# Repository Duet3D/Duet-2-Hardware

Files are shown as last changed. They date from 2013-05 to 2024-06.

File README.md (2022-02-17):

# Duet-2-Hardware

The Duet 2 3D Printer Controller design files repository.

For hardware ourhcases see https://www.duet3d.com/

Duet Hardware runs RepRapFirmware:
https://github.com/Duet3D/RepRapFirmware

Documentation:
https://docs.duet3d.com/Duet3D_hardware/Duet_2_family

## Duet 2 Wifi and Duet 2 Ethernet

Design by Tony Lock and David Crocker
More info:
https://www.duet3d.com/
LICENSE: see the LICENSE file in the repository

## Duet 0.8.5

Design by Tony Lock, based on the Duet 0.6
More info here:
http://blog.think3dprint3d.com/2015/08/new-duet-electronics-version-085.html
LICENSE: http://www.ohwr.org/attachments/2388/cern_ohl_v_1_2.txt

## Duet 0.6:
Design by Andy Hingston, Tony Lock, Adrian Bowyer with much advice from Chris Palmer.
More info here:
http://blog.think3dprint3d.com/2013/12/Duet-Arduino-Due-compatible-3DPrinter-controller.html
LICENSE: http://www.ohwr.org/attachments/2388/cern_ohl_v_1_2.txt

Developed in KiCAD: http://www.kicad-pcb.org/display/KICAD/KiCad+EDA+Software+Suite

## Support requests

Please use the [forum](https://forum.duet3d.com) for support requests.

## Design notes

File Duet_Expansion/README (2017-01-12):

For info on the Duex2/5 see:
https://duet3d.com/wiki/Duex2_and_Duex5_Features

For more info on the Duex4 expansion board see:
http://blog.think3dprint3d.com/2015/04/duex4-v02a-minor-updates.html

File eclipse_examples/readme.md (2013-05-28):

Example Eclipse projects for Arduino Due 

Eclipse version Juno SR1, CDT 8.1.1

ArduinoDueCore should be in the Eclipse Workspace along with other 
Eclipse Due projects which reference this Core project - this allows
for easily debugging by following what core functions do.

The DueTemplate project is a simple "hello world"/blink project which
is easy to copy and adapt for other projects as it is setup with the
required libraries and toolchain directories

The SD_HSMCI_TEST project provides the same functionality as the
hsmci_example sketch within ..\test_sketches\hsmci_example. It writes
and reads a number of test files to an SD card.

The steps to integrate Due into Eclipse is based on the forum posts
here:
http://forum.arduino.cc/index.php/topic,135403.0.html
especially the posts by Nassarane

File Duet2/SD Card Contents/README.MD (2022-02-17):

This is the SD card contents distributed with Duet Generation 2 (Duet Wifi and Duet Ethernet) boards as at May 2019

The SD card contents are only a starting point and the files in the /sys directory should be updated to match a specific printer configuration. A good start point for this is the RepRapFirmware configurator:

https://configtool.reprapfirmware.org/

For more information on the SD card structure check:
https://docs.duet3d.com/en/User_manual/RepRapFirmware/SD_card

For updating the firmware this is a good start point:
https://docs.duet3d.com/en/User_manual/RepRapFirmware/Updating_firmware

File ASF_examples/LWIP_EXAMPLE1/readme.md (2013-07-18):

Example ATMEL Studio 6.1 project for using the SAM3X8E and the KSZ8051RNL PHY
Modifications by tony@think3dprint3d.com, Based on the Atmel Studio Framework example
project for LWIP on the SAM3X8H development board.

All code (c) the respective owners as noted in the header files.

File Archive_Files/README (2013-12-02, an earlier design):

Note about the archive files specifically.

These files consist of test programs for Arduino IDE, Eclipse and Atmel Studio Framework. They are mainly based on example code from ASF, along with some original work by Tony@think3dprint3d.com. Where not specified they are licensed under the GPL v3.0 (but the vast majority has specified licenses from ASP or elsewhere).

Quite a lot of these programs and bits of code were designed to work on older versions of the DUET and may not work with the current version.
Tony Lock
blog.think3dprint3d.com

--------------------

Duet test arduino code in \test_sketches, libraries for duet specific peripherals in \libraries (now out of date)

The LwIP example has only been tested in Atmel Studio 6 and is adapted from the SAM3X-EK example
in the Atmel Studio Framework. It sets up a basic TCP/IP stack which responds to ping and serves
a single webpage on 192.168.0.100

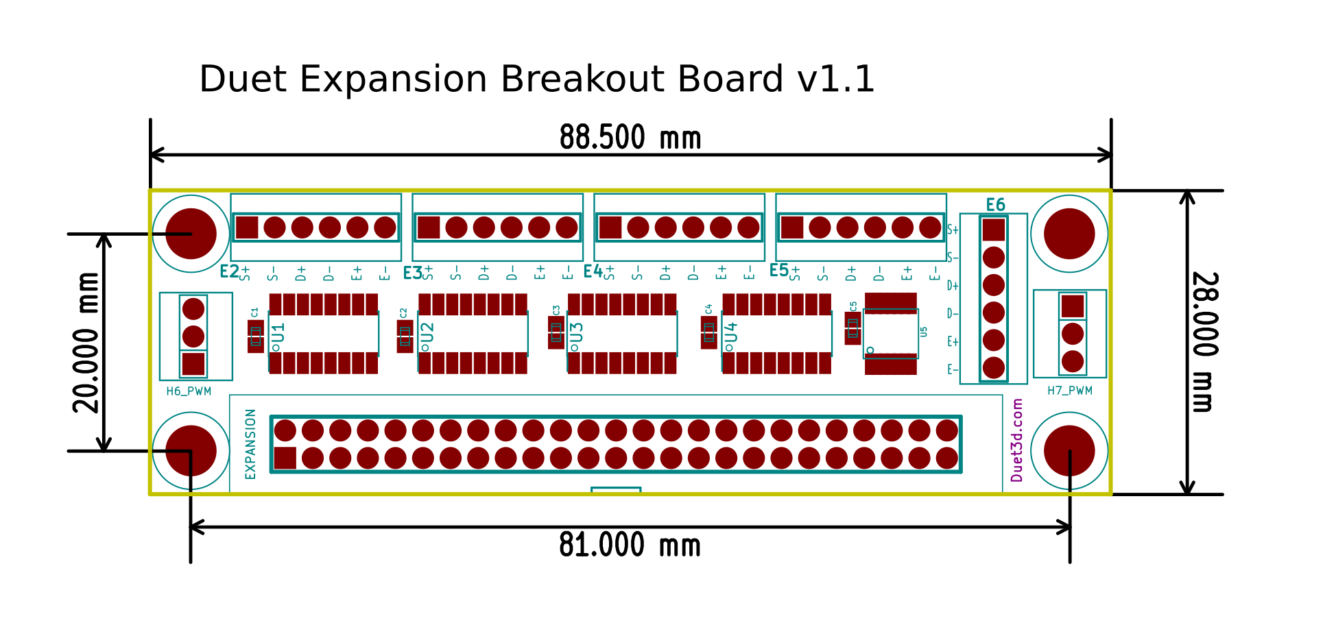
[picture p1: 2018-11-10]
Duet_Expansion/Expansion_Breakoutv1.1/ExpBreakoutv1.1_Dimensions.png

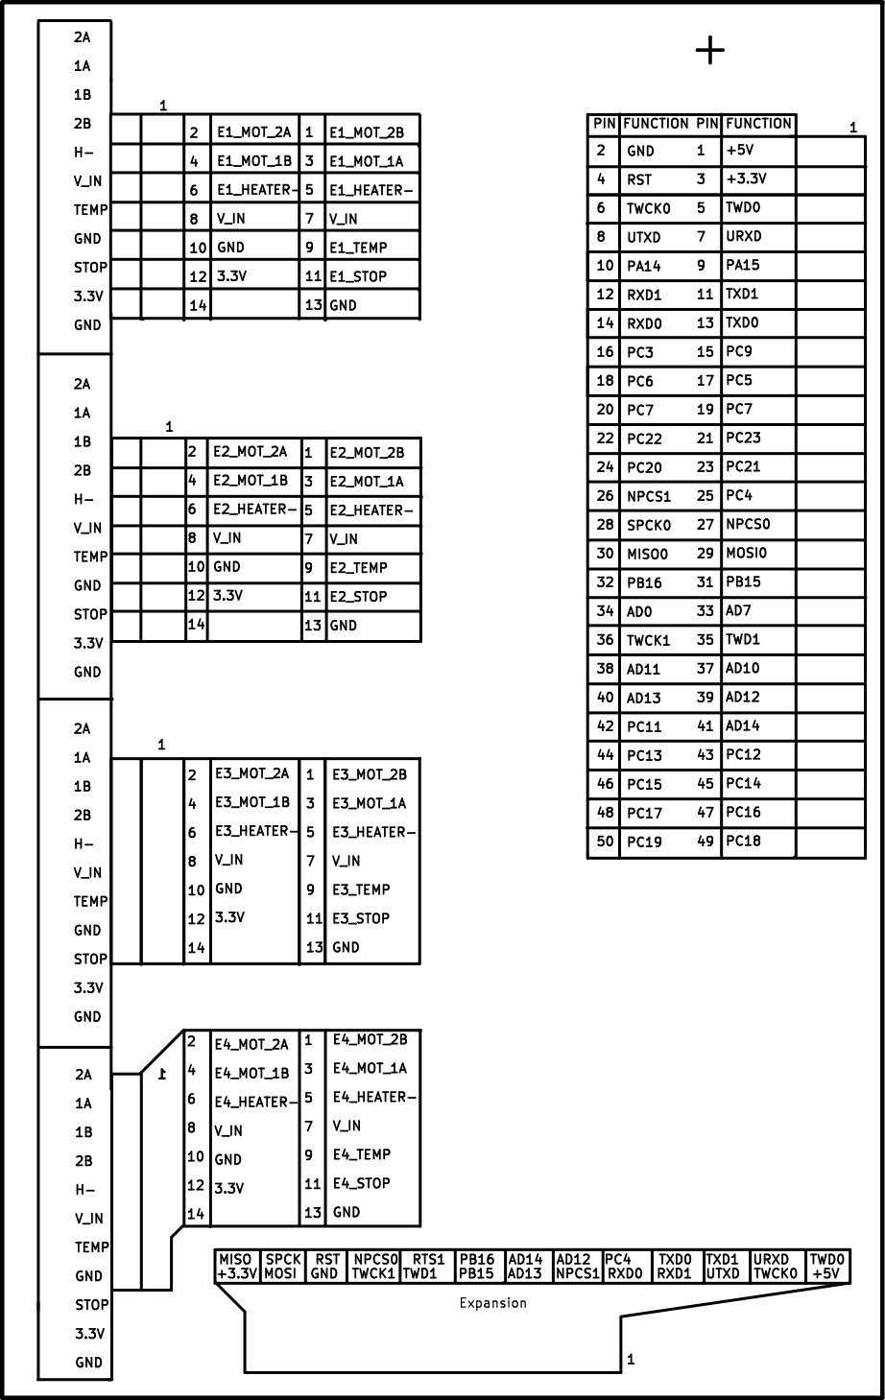
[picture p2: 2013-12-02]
Duet_Expansion/Duex4v0.2/back_silkscreen.png

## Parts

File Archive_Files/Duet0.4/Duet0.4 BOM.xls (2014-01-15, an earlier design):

Part / Value | Qty | Package | Manufacturer / Part No. | Circuit Reference
Resistors, Thick Film
0R1, 1% | 8 | 1206 | Any | R32, R33, R34, R35, R44, R45, R46, R47
33R, 1% | 7 | 0603 | Any | R2, R3, R6, R7, R8, R9, R10
100R, 1% | 4 | 0603 | Any | R56, R57, R58, R59
220R, 1% | 2 | 0603 | Any | R16, R17
1k, 1% | 4 | 0603 | Any | R11, R18, R22, R24
1k5, 1% | 2 | 0603 | Any | R1, R64
4k7, 1% | 8 | 0603 | Any | R12, R13, R14, R19, R21, R65, R67, R68
6k49, 1% | 1 | 0603 | Any | R15
10k, 1% | 22 | 0603 | Any | R5, R20, R23, R25, R27, R29, R30, R31, R39, R41, R42, R43, R50, R51, R52, R53, R54, R55, R60, R61, R62, R63
12k, 1% | 4 | 0603 | Any | R36, R37, R48, R49
15k, 1% | 1 | 0603 | Any | R4
100k, 1% | 4 | 0603 | Any | R26, R28, R38, R40
Capacitors, Ceramic
22p, 50V, C0G/NP0, 5% | 4 | 0603 | Any | C8, C9, C44, C45
0u01, 50V, X7R, 10% | 1 | 0603 | Any | C47
0u1, 50V, X7R, 10% | 24 | 0603 | Any | C1, C5, C16, C17, C24, C25, C28, C29, C34, C35, C38, C39, C40, C41, C42, C43, C46, C48, C49, C50, C51, C52, C53, C55
0u22, 50V, X7R, 10% | 8 | 0603 | Any | C20, C21, C26, C27, C30, C31, C36, C37
2u2, 10V, X7R, 10% | 1 | 0805 | Any | C12
10u, 10V, X5R, 10% | 4 | 0805 | Any | C4, C7, C18, C19
22u, 6.3V, X7R, 10% | 2 | 1210 | Any | C10, C11
Capacitors, Al Electrolytic
100u, 35V, 20% | 6 | 6.3 x 7.7mm | Any | C3, C22, C23, C32, C33, C54
100u, 25V, 20% | 1 | 6.3 x 7.7mm | EPCOS, B41142A5107M | C6
Inductors / Filters
Power, 150uH, 0.5A | 1 | 2424 | PANASONIC - ELL6UH151M | L1
Ferrite Bead, 470R, 100Mhz | 2 | 0603 | Any | L3, L4
Ferrite Bead, 100R, 100MHz | 1 | 1206 | Any | L2
Crystals
12MHz | 1 | 5 x 3.2mm | TBD | X2
25MHz | 1 | 5 x 3.2mm | TBD | X1
Diodes
TS4148 | 2 | 0805 | Taiwan Semi - TS4148 RY | D4, D5
SS14M | 2 | uSMA | Taiwan Semi - SS14M | D1, D2
LED, 2mA, 1.8V | 4 | 0603 | Vishay - TLMO1000-GS08 | D3, D6, D7, D8
FETs
N-Ch, 20V, Logic-level | 3 | SOT-23 | NXP - BSH105 | TR1, TR3, TR5
P-Ch, 50V, Logic-level | 1 | SOT-23 | NXP - BSS84AK | TR7
N-Ch, 40V, Power | 3 | DPAK / TO-252 | Infineon - IPD036N04L | TR2, TR4, TR6
ICs
LPC1768 | 1 | LQFP100 | NXP - LPC1768FBD100,551 | U1
A4982 | 4 | TSSOP-24 | Allegro - A4982SLPTR-T | U5, U6, U7, U8
LM2594 | 1 | SOIC-8 | Nat Semi - LM2594M-5.0 | U3
LM1117 | 1 | SOT-223 | Nat Semi - LM1117MP-3.3 | U2
MCP44X1 | 1 | TSSOP-20 | Microchip - MCP4461-103E/ST | U9
KSZ8051 | 1 | QFN-32 | Micrel - KSZ8051RNL TR | U4
Miscellaneous
Micro Push Button Switch | 2 | SMD | Panasonic - EVQQ2T03W | S1, S2
USB - Micro B | 1 | SMD | FCI - 10118192-0001LF | J22
Micro SD Card Slot | 1 | SMD | TBD | J18
Connectors
RJ45+MAG | 1 |  |  | J19
BED_HEATER | 1 |  |  | J4
BED_TEMP | 1 |  |  | J5
CONN2X13 | 1 |  |  | J2
CONN2X20 | 2 |  |  | J1, J6
CONN_JTAG | 1 |  |  | J21
E0_HEATER | 1 |  |  | J11
E0_MOT/STOP | 1 |  |  | J10
E0_TEMP | 1 |  |  | J12
FAN0 | 1 |  |  | J13
I2C_2 | 1 |  |  | J3
JUMPER | 8 |  |  | JP1, JP2, JP3, JP4, JP5, JP6, JP7, JP8
POWER_IN | 1 |  |  | J23
UART0 | 1 |  |  | J20
X_MOT/STOP | 1 |  |  | J9
Y_MOT/STOP | 1 |  |  | J8
Z_MOT/STOP | 1 |  |  | J7

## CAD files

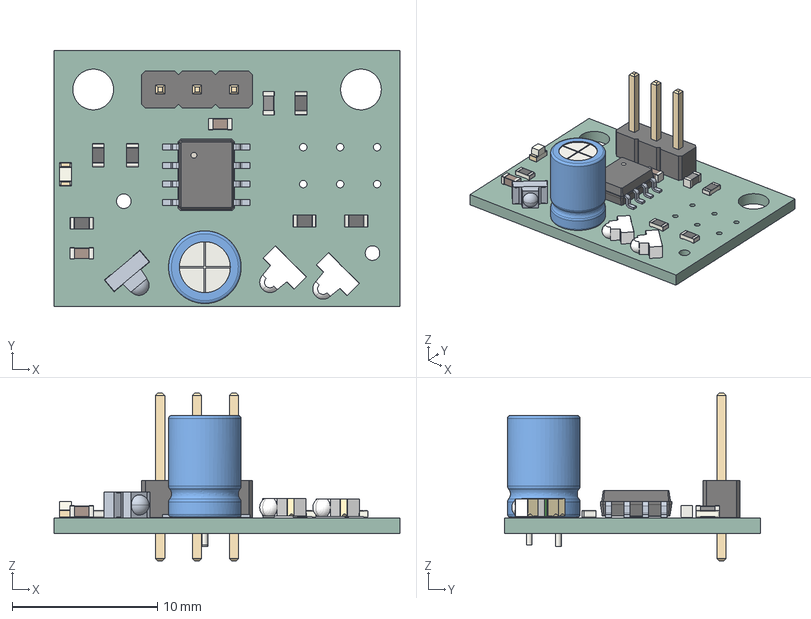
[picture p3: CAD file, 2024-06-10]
Duet_Expansion/MiniLedSensor.stp
23.8 x 17.6 x 11.5 mm
_autosave-MiniLedSensor PCB

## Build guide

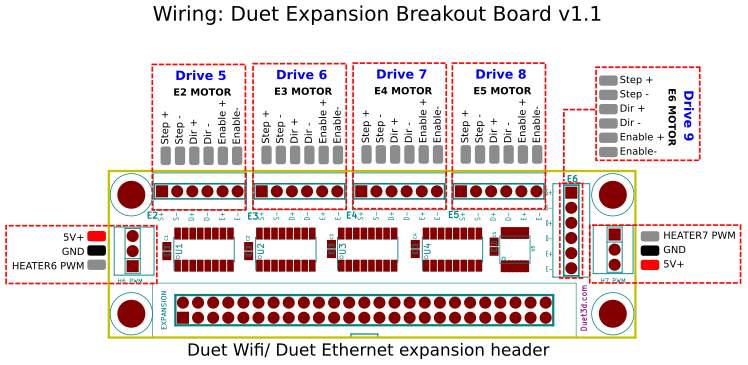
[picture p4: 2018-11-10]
Duet_Expansion/Expansion_Breakoutv1.1/ExpBreakoutv1.1_Wiring.png

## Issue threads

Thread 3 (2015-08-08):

missing component libraries

woodsmoke, 2015-08-08:
Where does one get hold of special.lib component library in order to properly open the Duet0.85.sch schematic?

T3P3, 2015-08-08:
Hi woodsmoke, I guess its a KiCAD library as all the custom parts for the board are in the FE.lib (and should be cached in  Duet0.85-cache.lib as well).
Have you tried looking in the KiCAD install path/share/Library for special.lib? Alternatively you can remove it from the list of libraries associated with the project within eschema using the library editor.

Tony

woodsmoke, 2015-08-08:
KiCAD received a rather thorough overhaul recently. Library files are all .pretty now I think. I'll try some older versions. Thanks.

Closed 2015-08-08.

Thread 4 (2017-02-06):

Adapting Duet Wifi design for a Teensy 3.6 based controller board

Flydroid, 2017-02-06:
Hi Tony,

I'm currently designing a 3D printer controller Board which is based on the[ Teensy 3.6.](https://www.pjrc.com/teensy/techspecs.html).

For my motivation, i have to say that there isn't a 3d printer controller for the Teensy yet and the new TMC2130 haven't been used with all it s features.  The board should follow the ramps principle, you plug in the microcontroller board and the stepper drivers, here the Teensy 3.6 and the TMC2130 SilentStepSticks.
My current featureset:
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

On the software side there are some developments for Marlin on Teensy 3.6 but dc42 also [said](http://forums.reprap.org/read.php?13,711399) that a port of Raprap Firmware HAL CoreNG might be doable.

I really like the feature set of the  DuetWifi, as it is appropriate to the current 32bit mcus.
You have published the DuetWifi hardware  files under the Cern OHL 1.2.  I've read the License and  howto from cern. but I'm inexperienced in the open hardware sector.

Would it be possible to base some of my schematics (mosfet endstop) on the duetwifi when giving the appropriate credit following the Cern OHL v1.2? And of course releasing the source on Github.

Best Regards
Jonathan

T3P3, 2017-02-07:
Hi Jonathan

That looks interesting and I saw the thread you linked to. If you port CoreNG to Teensy you then get to benefit from the rest of the RepRapFirmware which has a bunch of nice developments so well worth it.

Regarding the license question you are free to use the DuetWifi hardware design under the terms of the CERN OHL. In summary that means your new project should also be licensed under CERN OHL and the source files shared freely.

HTH, Tony

Flydroid, 2017-02-08:
Hi Tony,

That's great to hear. I will keep you updated!

I do have three questions about the duat wifi design:
- Why did you choose to use the 74HC125 spi buffer?
- What is the purpose of the caps (C91 - C94) beside de mosfets?
- Why didn't you use an extra diode to protect the endstop inputs in addition to the 10k resistor?

Best Regards
Jonathan

Yahchaan, 2018-02-04:
Did you look at the Trinamic TRAMS board SPI only? (On a MEGA) It can maybe help give direction.

Yahchaan, 2018-02-04:
You can download the Eagle files
https://github.com/trinamic/TRAMS

Yahchaan, 2018-07-10:
Did you do anything more? I cannot program, only do good PCB layout and need input - for I like the teensy

Flydroid, 2018-07-10:
Unfortunately I haven't been able to continue in the last months. Maybe
later this year.

Yahchaan <notifications@github.com> schrieb am Di., 10. Juli 2018, 17:05:

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

Closed 2019-10-09.

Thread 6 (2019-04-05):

"Mechanical" Drawings

Andy-ABTec, 2019-04-05:
Hi, is there a mechanical drawing available for the Duet 2?

I'm after board dimensions, mounting hole, ethernet connector and other opening positions to aid in case design.

Had a rummage through the code but couldn't spot anything...

Many thanks!

theopensourcerer, 2019-04-05:
I guess you will need KiCAD. Load the designs from the repository and then you can examine, measure and even print the PCB layout.

Probably from here: https://github.com/T3P3/Duet/tree/master/Duet2/Duet2v1.04

T3P3, 2019-04-05:
All our documentation is on Dozuki. Have a look here:
https://duet3d.dozuki.com/Wiki/Mounting_and_cooling_the_board
There are also 3D models linked from that page.

Andy-ABTec, 2019-04-05:
Thanks guys, sorry to have pestered...

Closed 2019-04-05.

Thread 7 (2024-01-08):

[FeatureRequest]: Add step files

boelle, 2024-01-08:
### Is your feature request related to a problem? Please describe.

i opened the duet 2  files and some step files are missing,

one example is the sd card reader

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

${KICAD6_3DMODEL_DIR}/Connector_SD.3dshapes/693071020811_Download_STEP_693071020811_rev1.stp

so that lead me to think that i need kicad6 as version 7 do not have the files

### Describe the solution you propose.

would be nice if any custom step files is added to a perfect representation in 3d could be made

or a note on how to get them

### Describe alternatives you've considered

having to install both the newest and and old version of kicad seems stupid to me

### Provide any additional context or information.

maybe this is just a luxuary problem

boelle, 2024-01-08:
i tried to install 6.0 and it does not have the step files, are they in a version between 6.0 and 7.0 ?

boelle, 2024-01-08:
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

i get that one when i try to save what is there as step

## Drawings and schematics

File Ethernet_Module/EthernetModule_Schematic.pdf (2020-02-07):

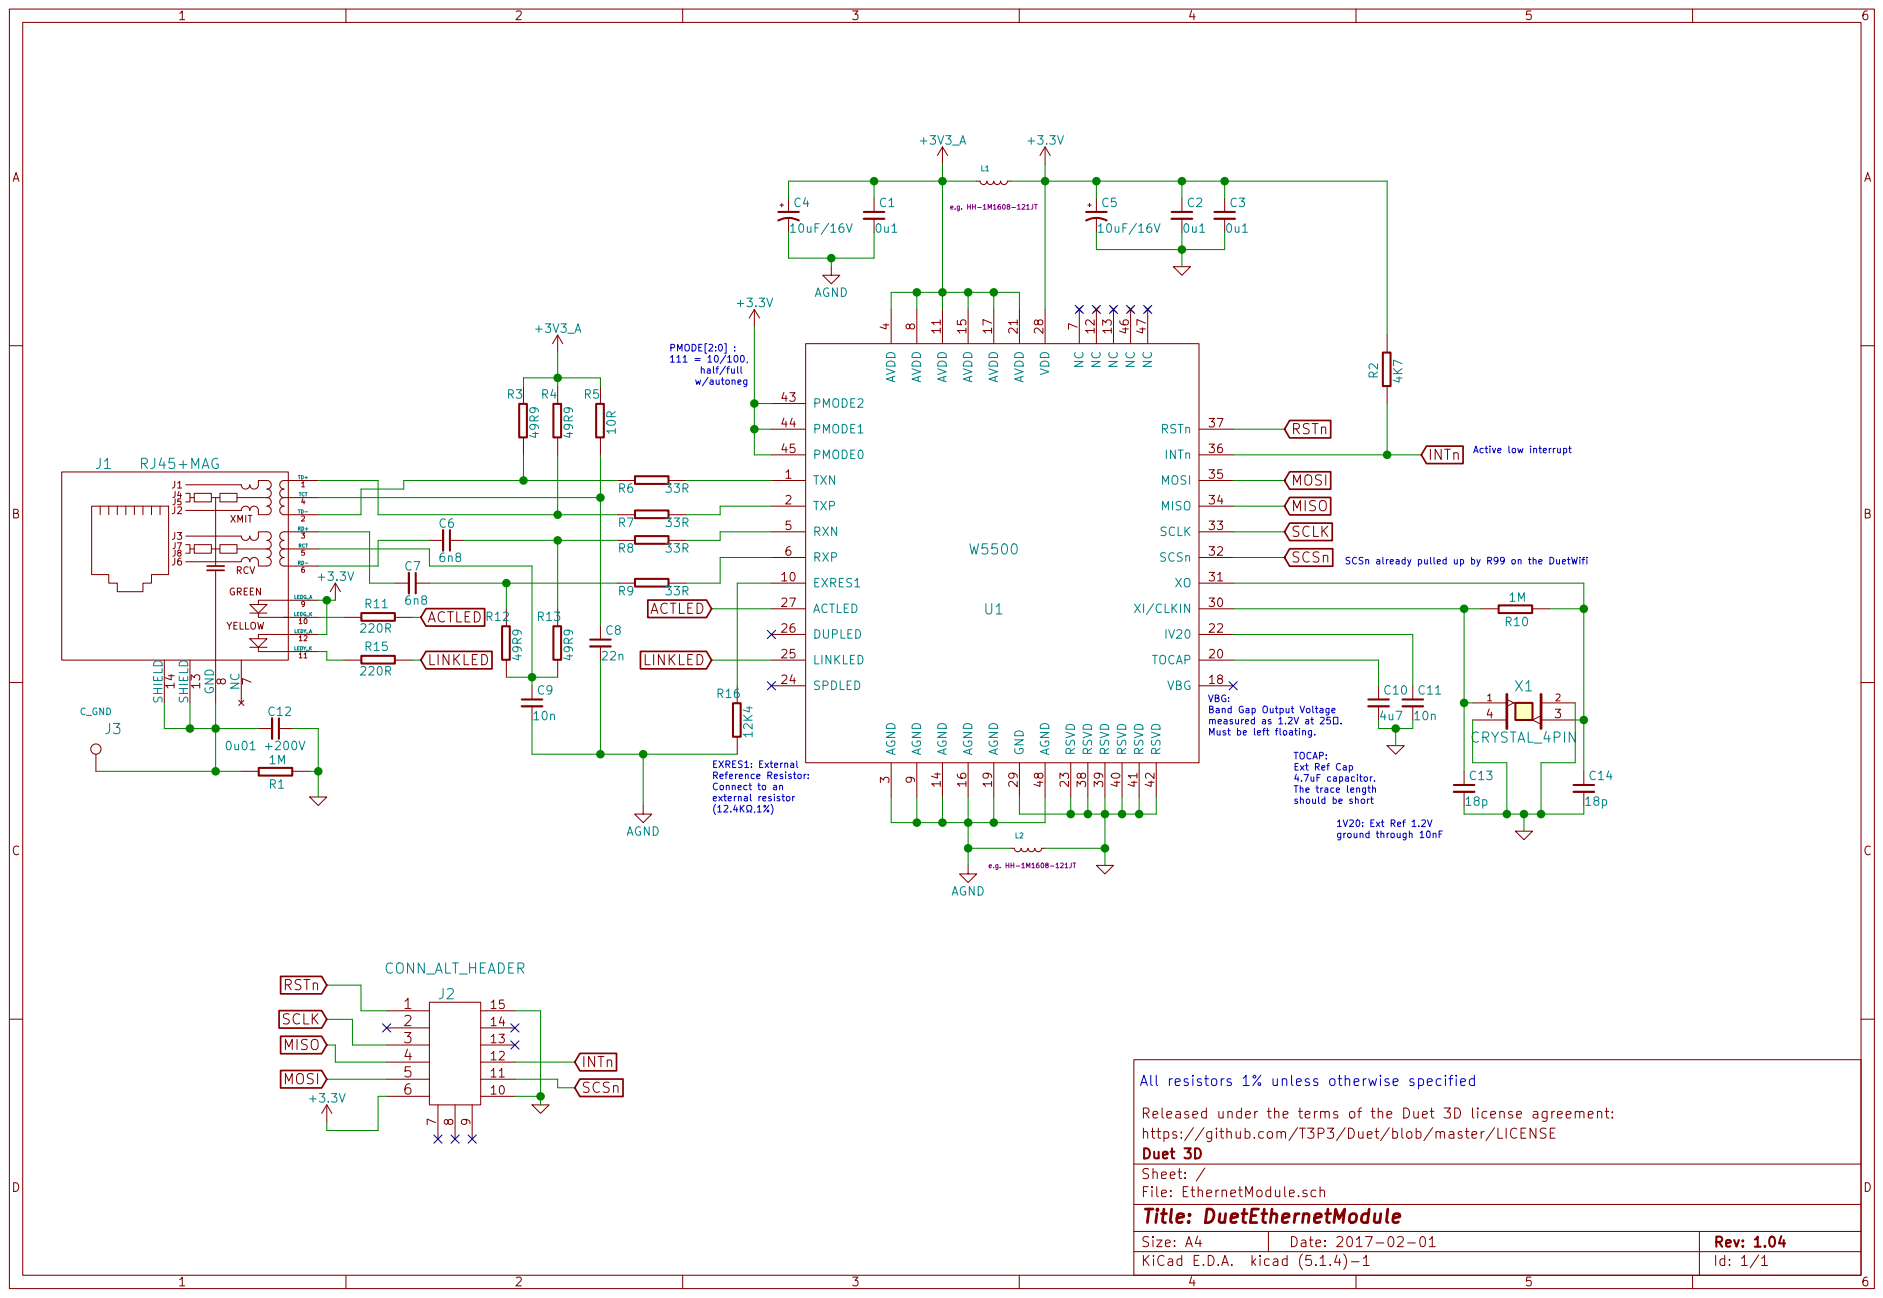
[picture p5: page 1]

4 RSVD 40 RSVD 41 RSVD 42 PMODE2 43 PMODE1 44 PMODE0 45 NC 46 NC 47 AGND 48 RXN 5 RXP 6 NC

3 XI/CLKIN 30 XO 31 SCSn 32 SCLK 33 MISO 34 MOSI 35

SCLK
SCSn
ground through 10nF SCSn already pulled up by R99 on the DuetWifi TOCAP: Ext Ref Cap

RD- 6 NC7 GND8 | 6n8 C7

VBG: Band Gap Output Voltage measured as 1.2V at 25. Must be left floating. EXRES1: External Reference Resistor: Connect to an

4.7uF capacitor. The trace length should be short All resistors 1% unless otherwise specified

Released under the terms of the Duet 3D license agreement: AGND

https://github.com/T3P3/Duet/blob/master/LICENSE
File: EthernetModule.sch Sheet: / Duet 3D

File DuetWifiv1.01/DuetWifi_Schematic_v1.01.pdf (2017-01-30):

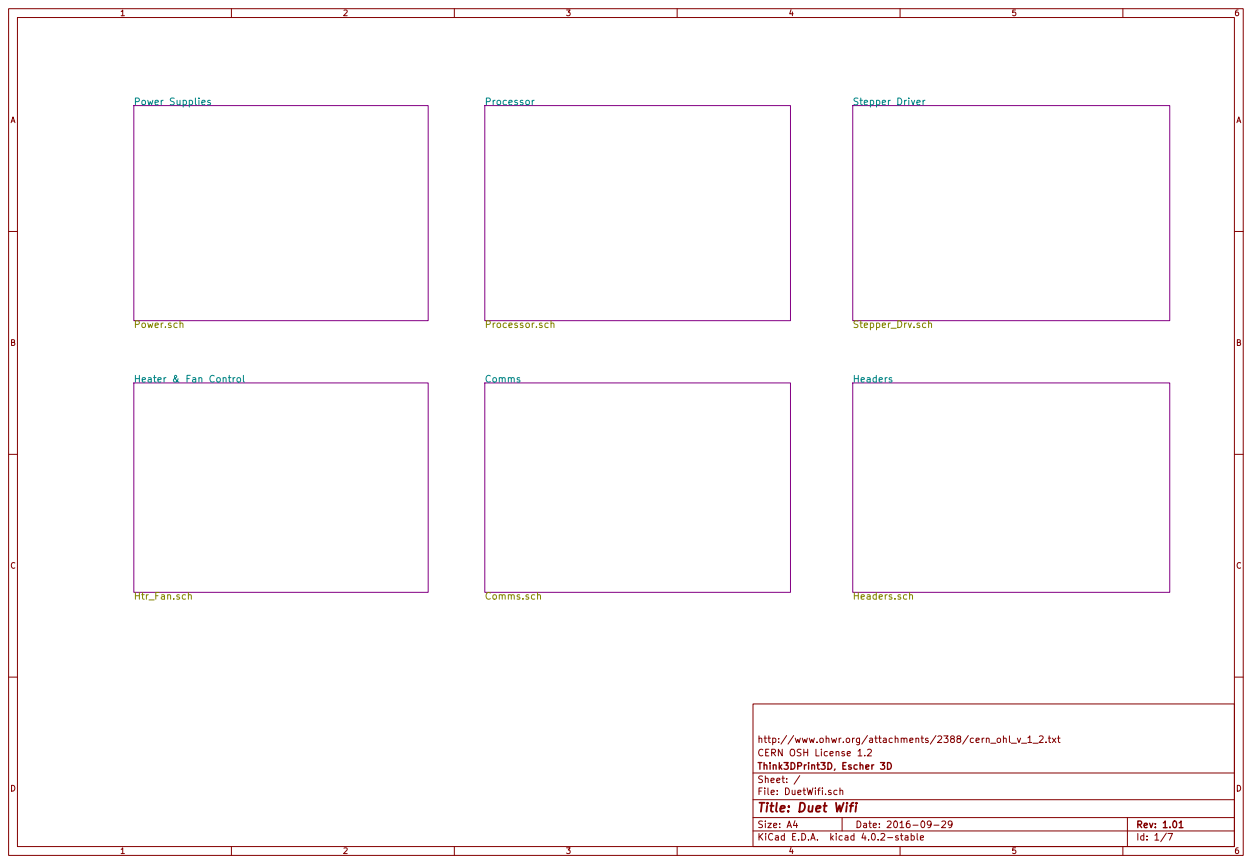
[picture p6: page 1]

http://www.ohwr.org/attachments/2388/cern_ohl_v_1_2.txt
CERN OSH License 1.2
Id: 1/7 Title: Duet Wifi File: DuetWifi.sch Sheet: / Think3DPrint3D, Escher 3D

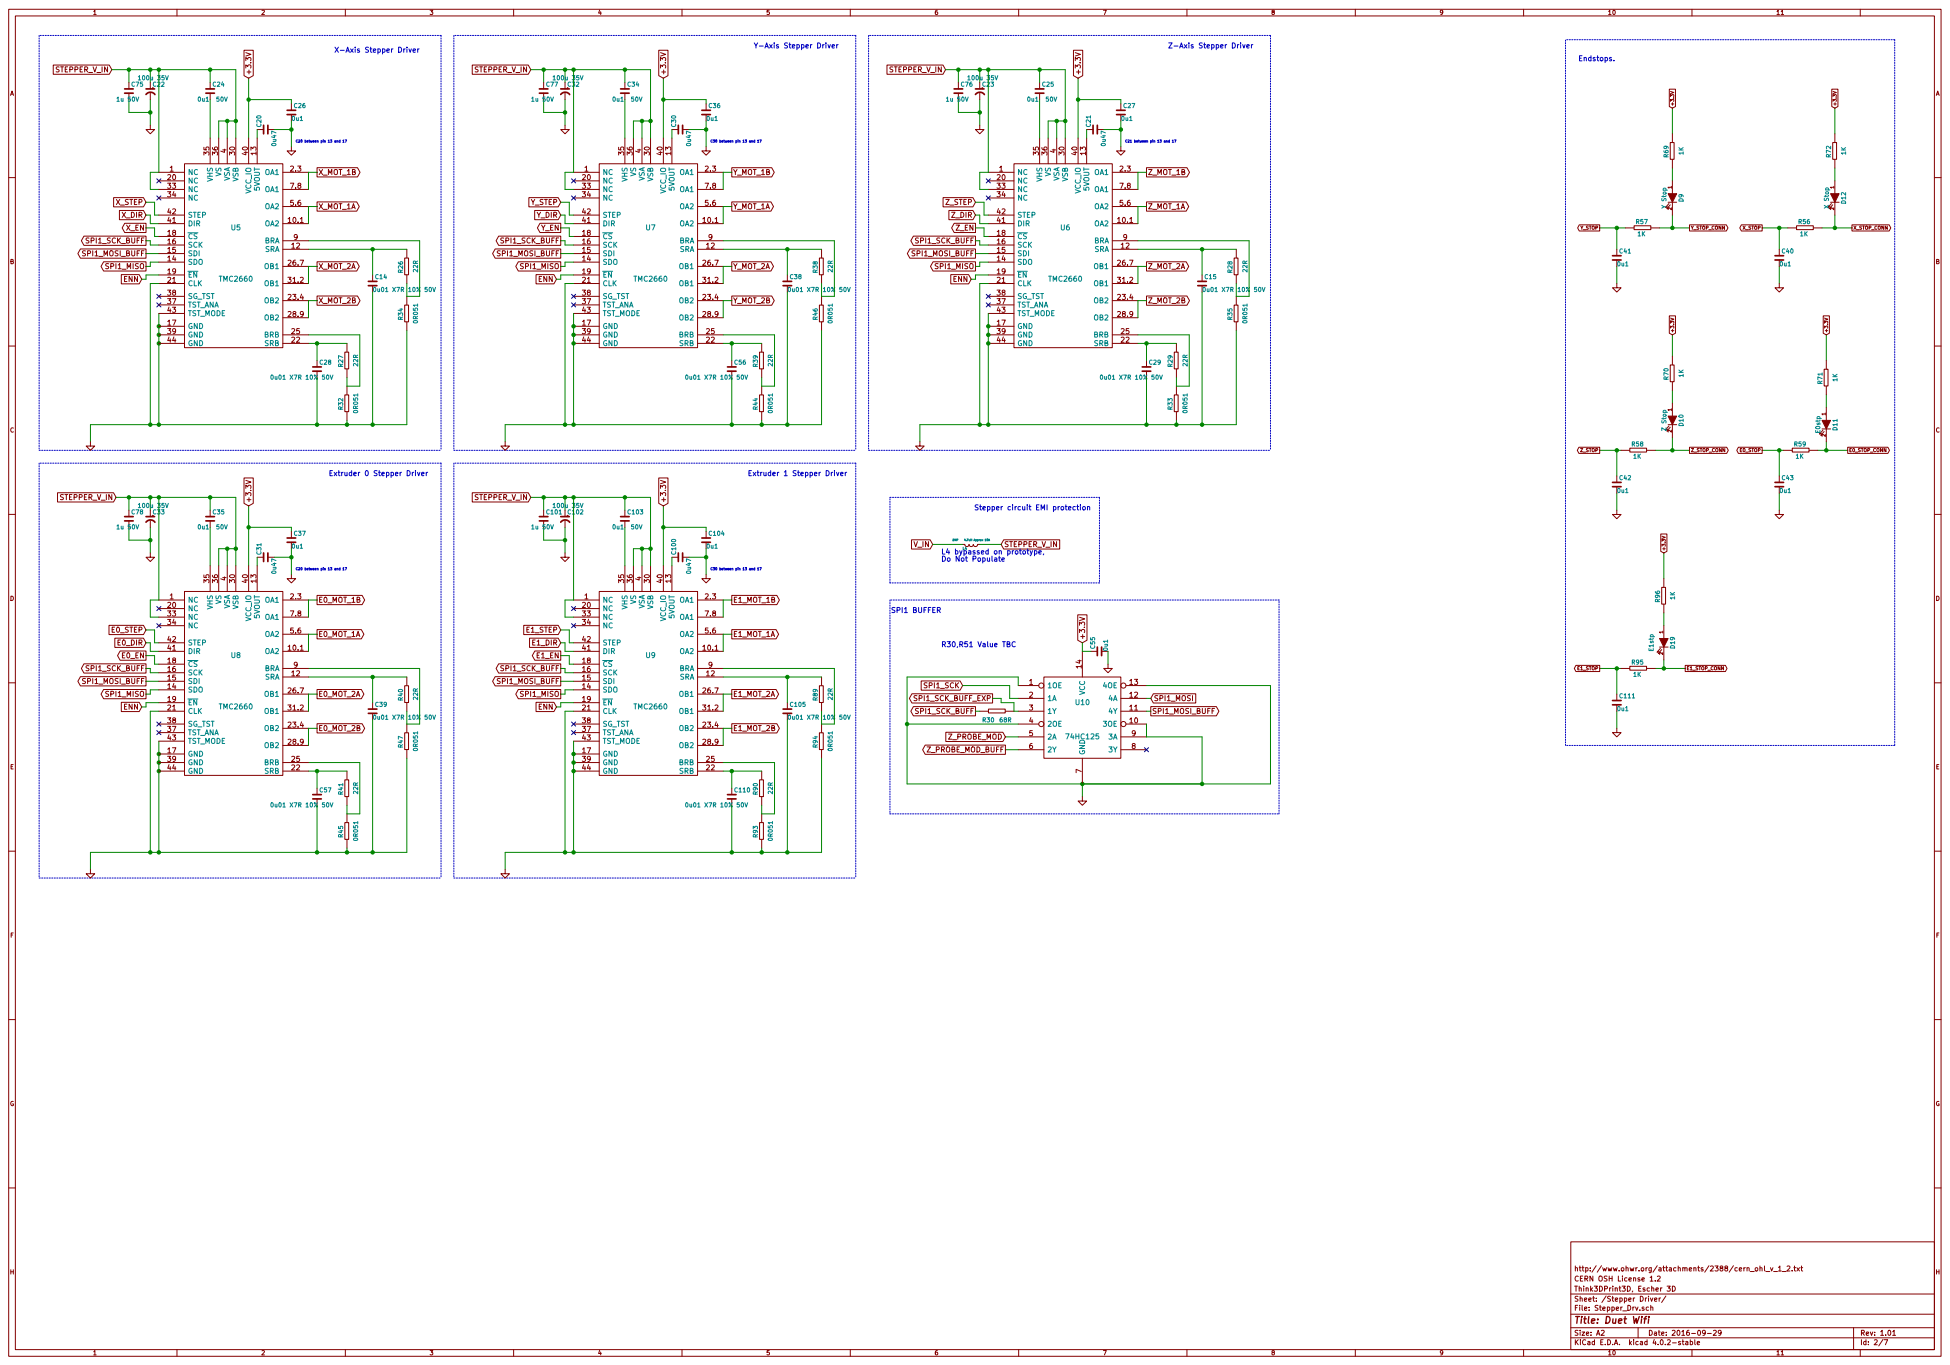
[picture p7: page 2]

Y-Axis Stepper Driver X-Axis Stepper Driver

Stepper circuit EMI protection

http://www.ohwr.org/attachments/2388/cern_ohl_v_1_2.txt
CERN OSH License 1.2
Think3DPrint3D, Escher 3D
Sheet: /Stepper Driver/
File: Stepper_Drv.sch
Id: 2/7 Title: Duet Wifi

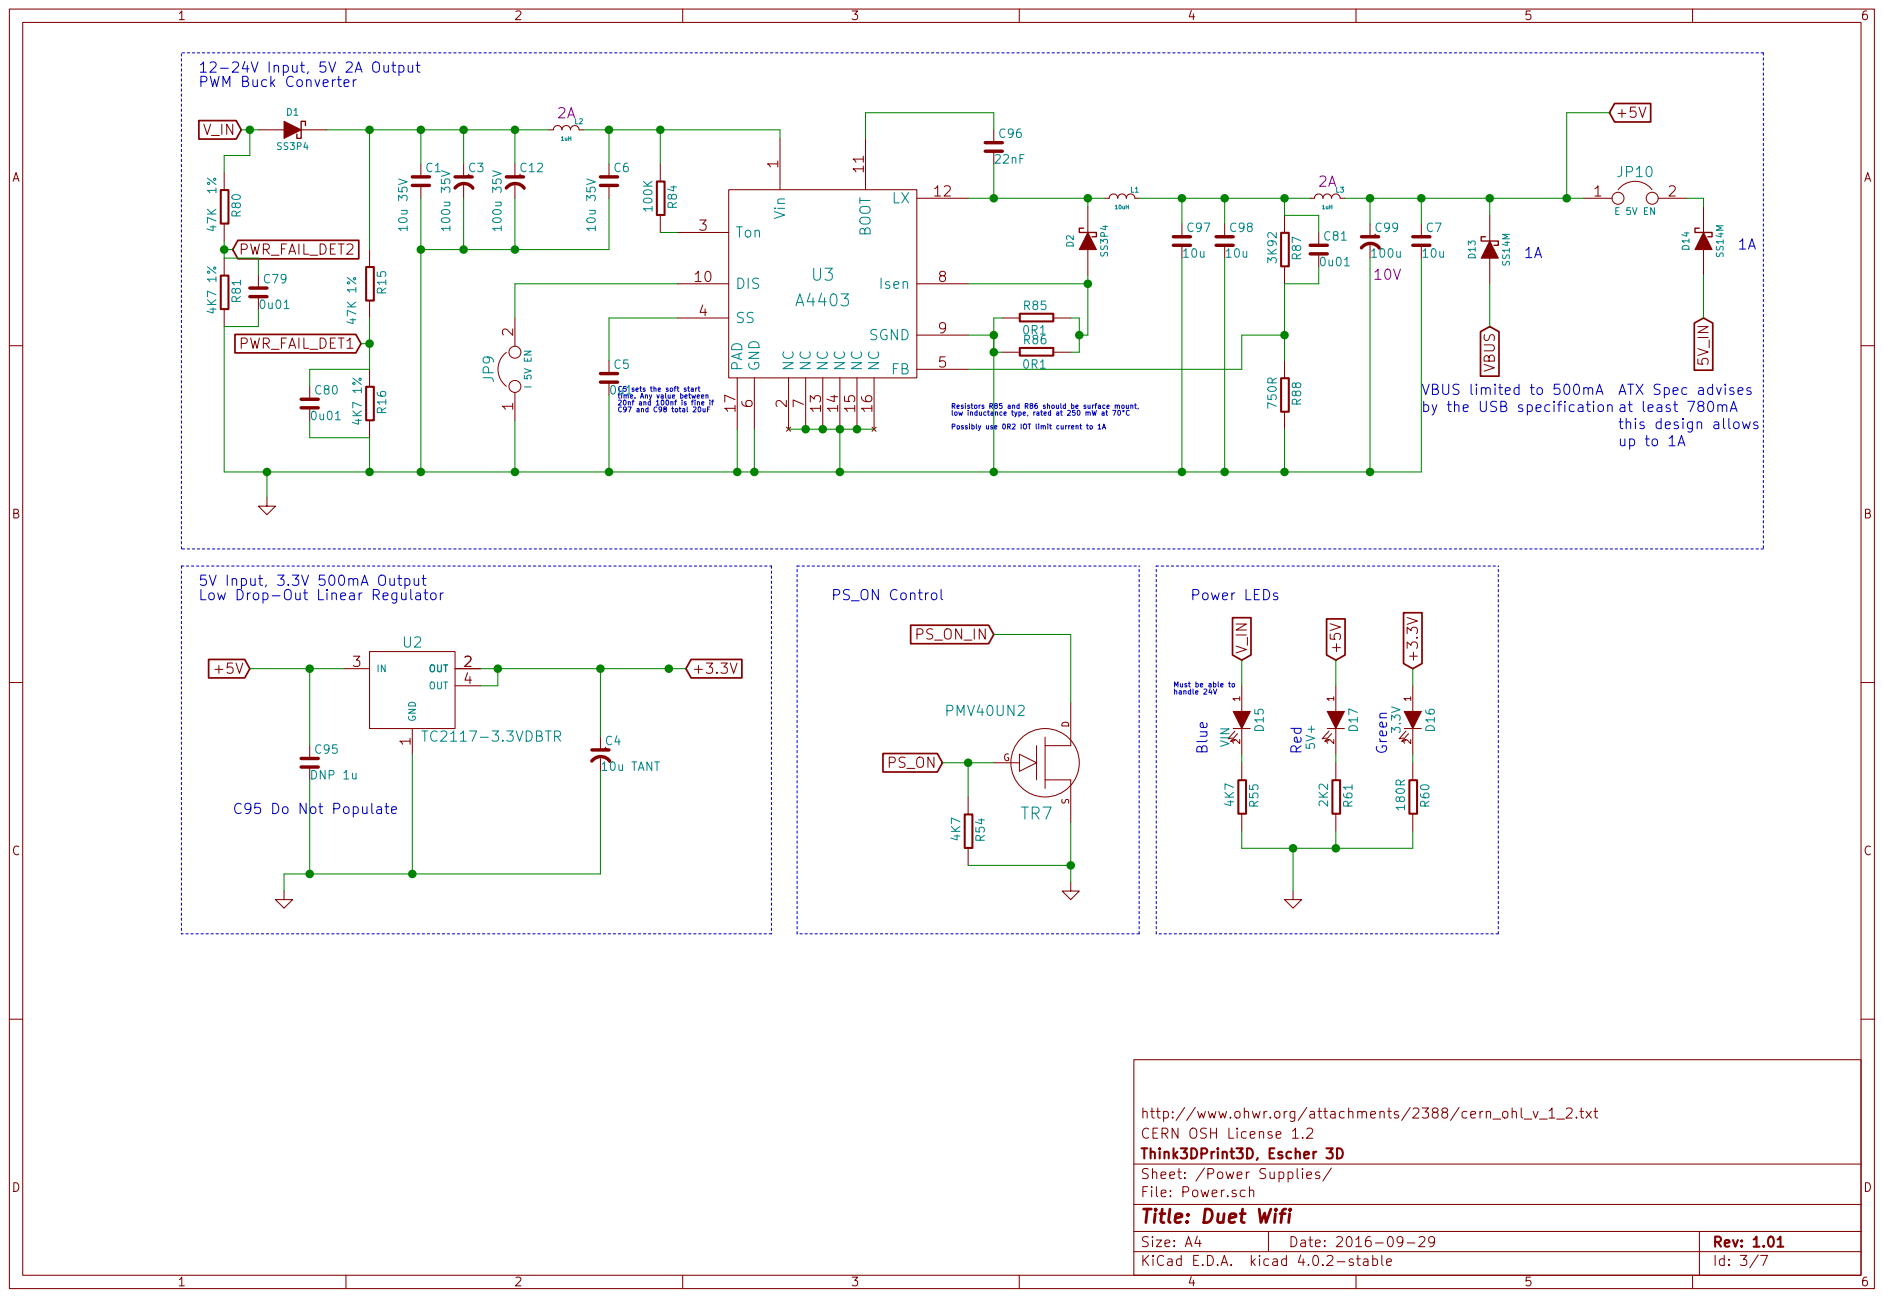
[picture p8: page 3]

U3 A4403 | LX | 12 NC 13 NC 14 NC 15 NC 16 PAD 17

2 Ton 3 SS 4 FB GND 5

Possibly use 0R2 IOT limit current to 1A C5 sets the soft start

time. Any value between

Resistors R85 and R86 should be surface mount,
low inductance type, rated at 250 mW at 70°C

by the USB specification

this design allows at least 780mA

5V Input, 3.3V 500mA Output
Low Drop-Out Linear Regulator

Must be able to

http://www.ohwr.org/attachments/2388/cern_ohl_v_1_2.txt
CERN OSH License 1.2
Think3DPrint3D, Escher 3D
Id: 3/7 Title: Duet Wifi File: Power.sch Sheet: /Power Supplies/

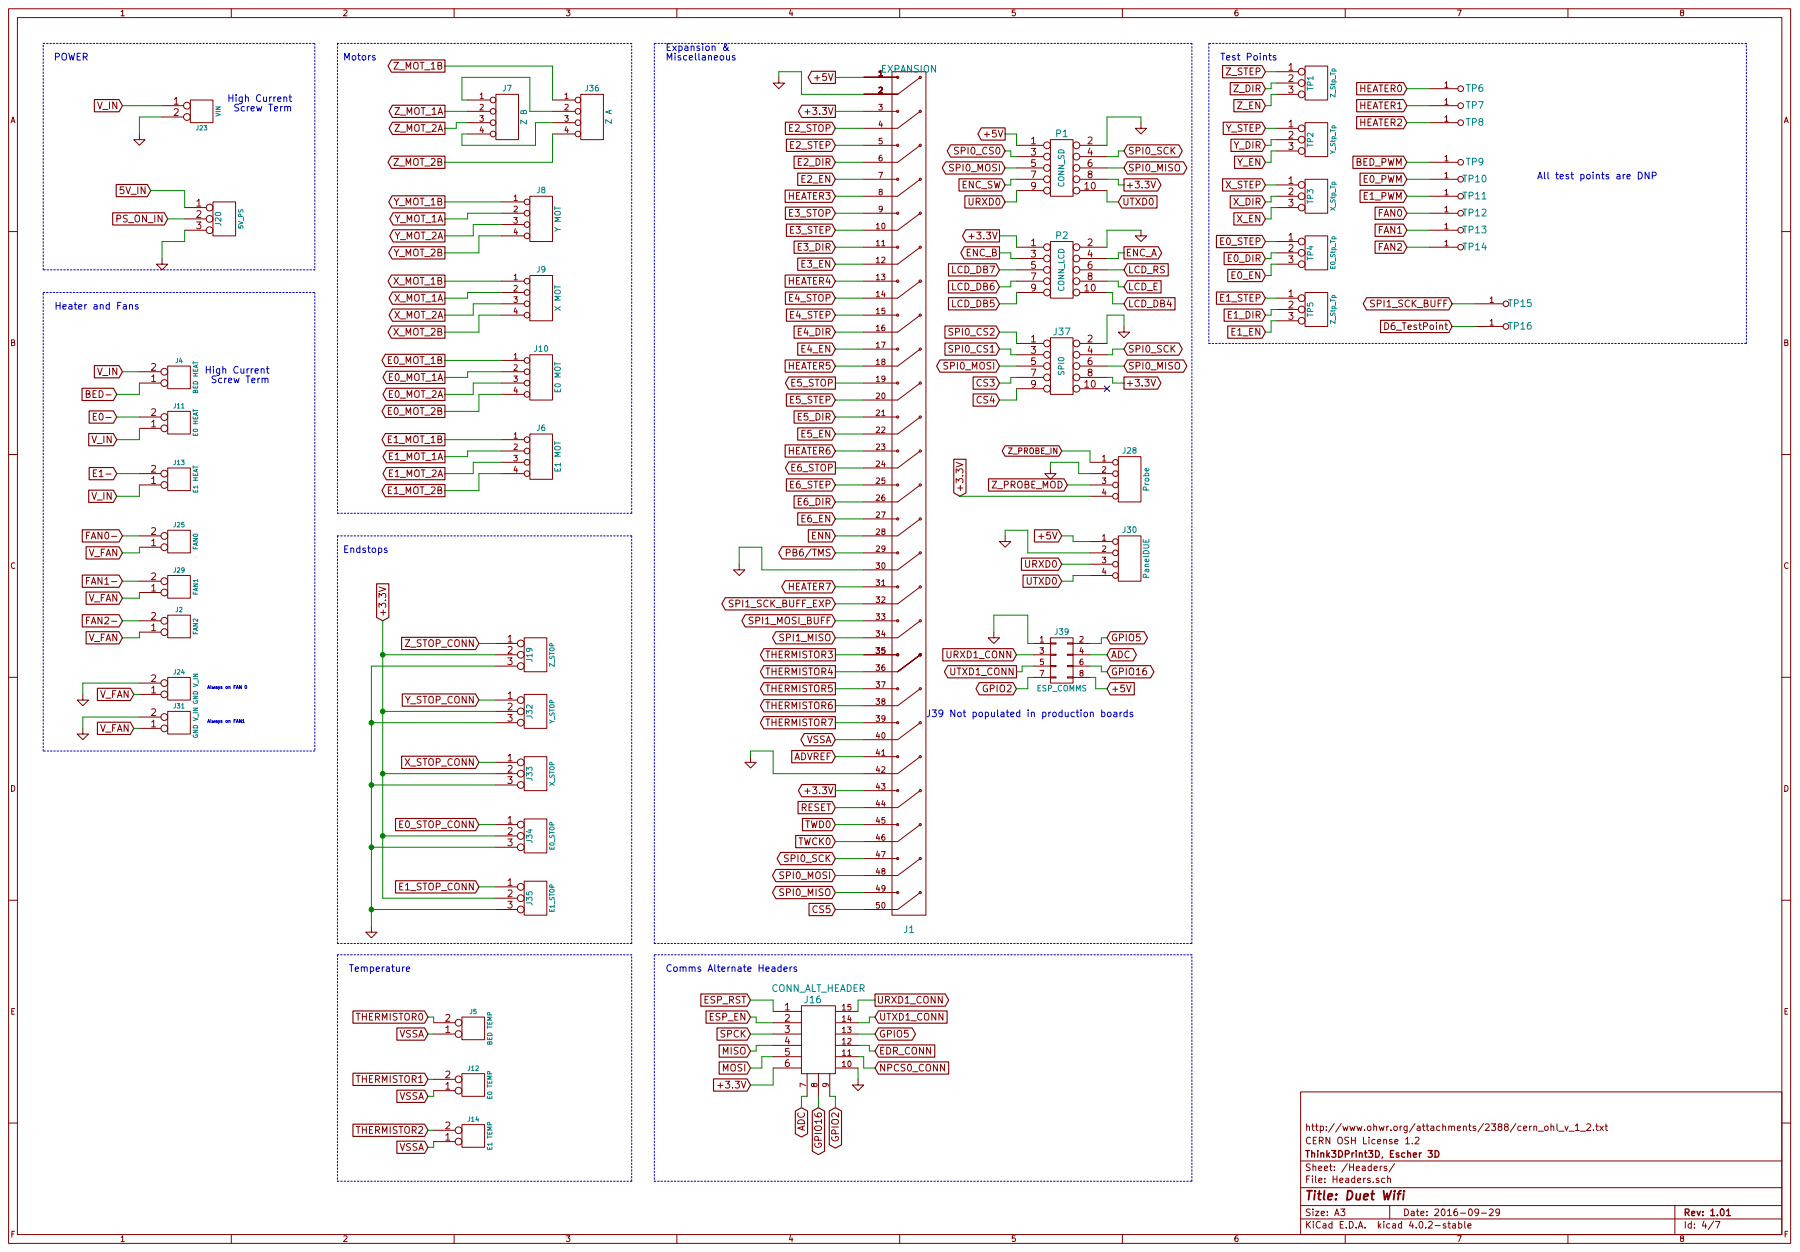
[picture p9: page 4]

J39 Not populated in production boards

CERN OSH License 1.2
Id: 4/7 Title: Duet Wifi File: Headers.sch Sheet: /Headers/ Think3DPrint3D, Escher 3D

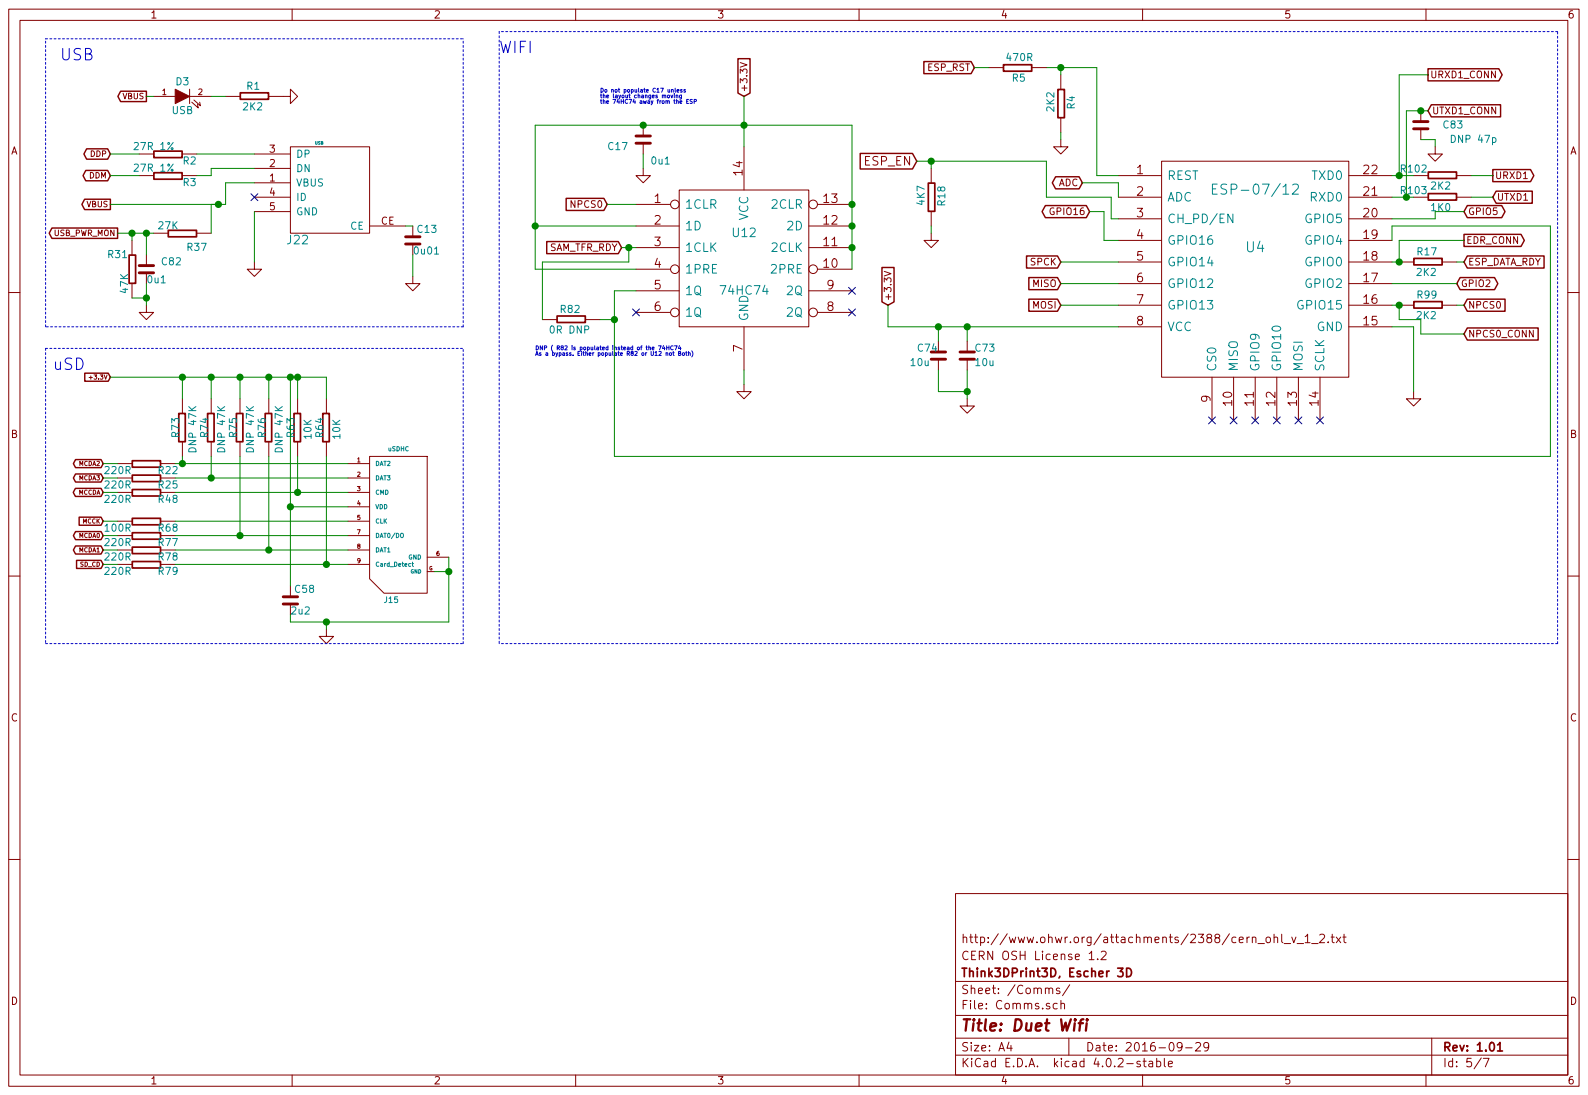
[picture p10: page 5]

Do not populate C17 unless
the layout changes moving

CERN OSH License 1.2
Id: 5/7 Title: Duet Wifi File: Comms.sch Sheet: /Comms/ Think3DPrint3D, Escher 3D

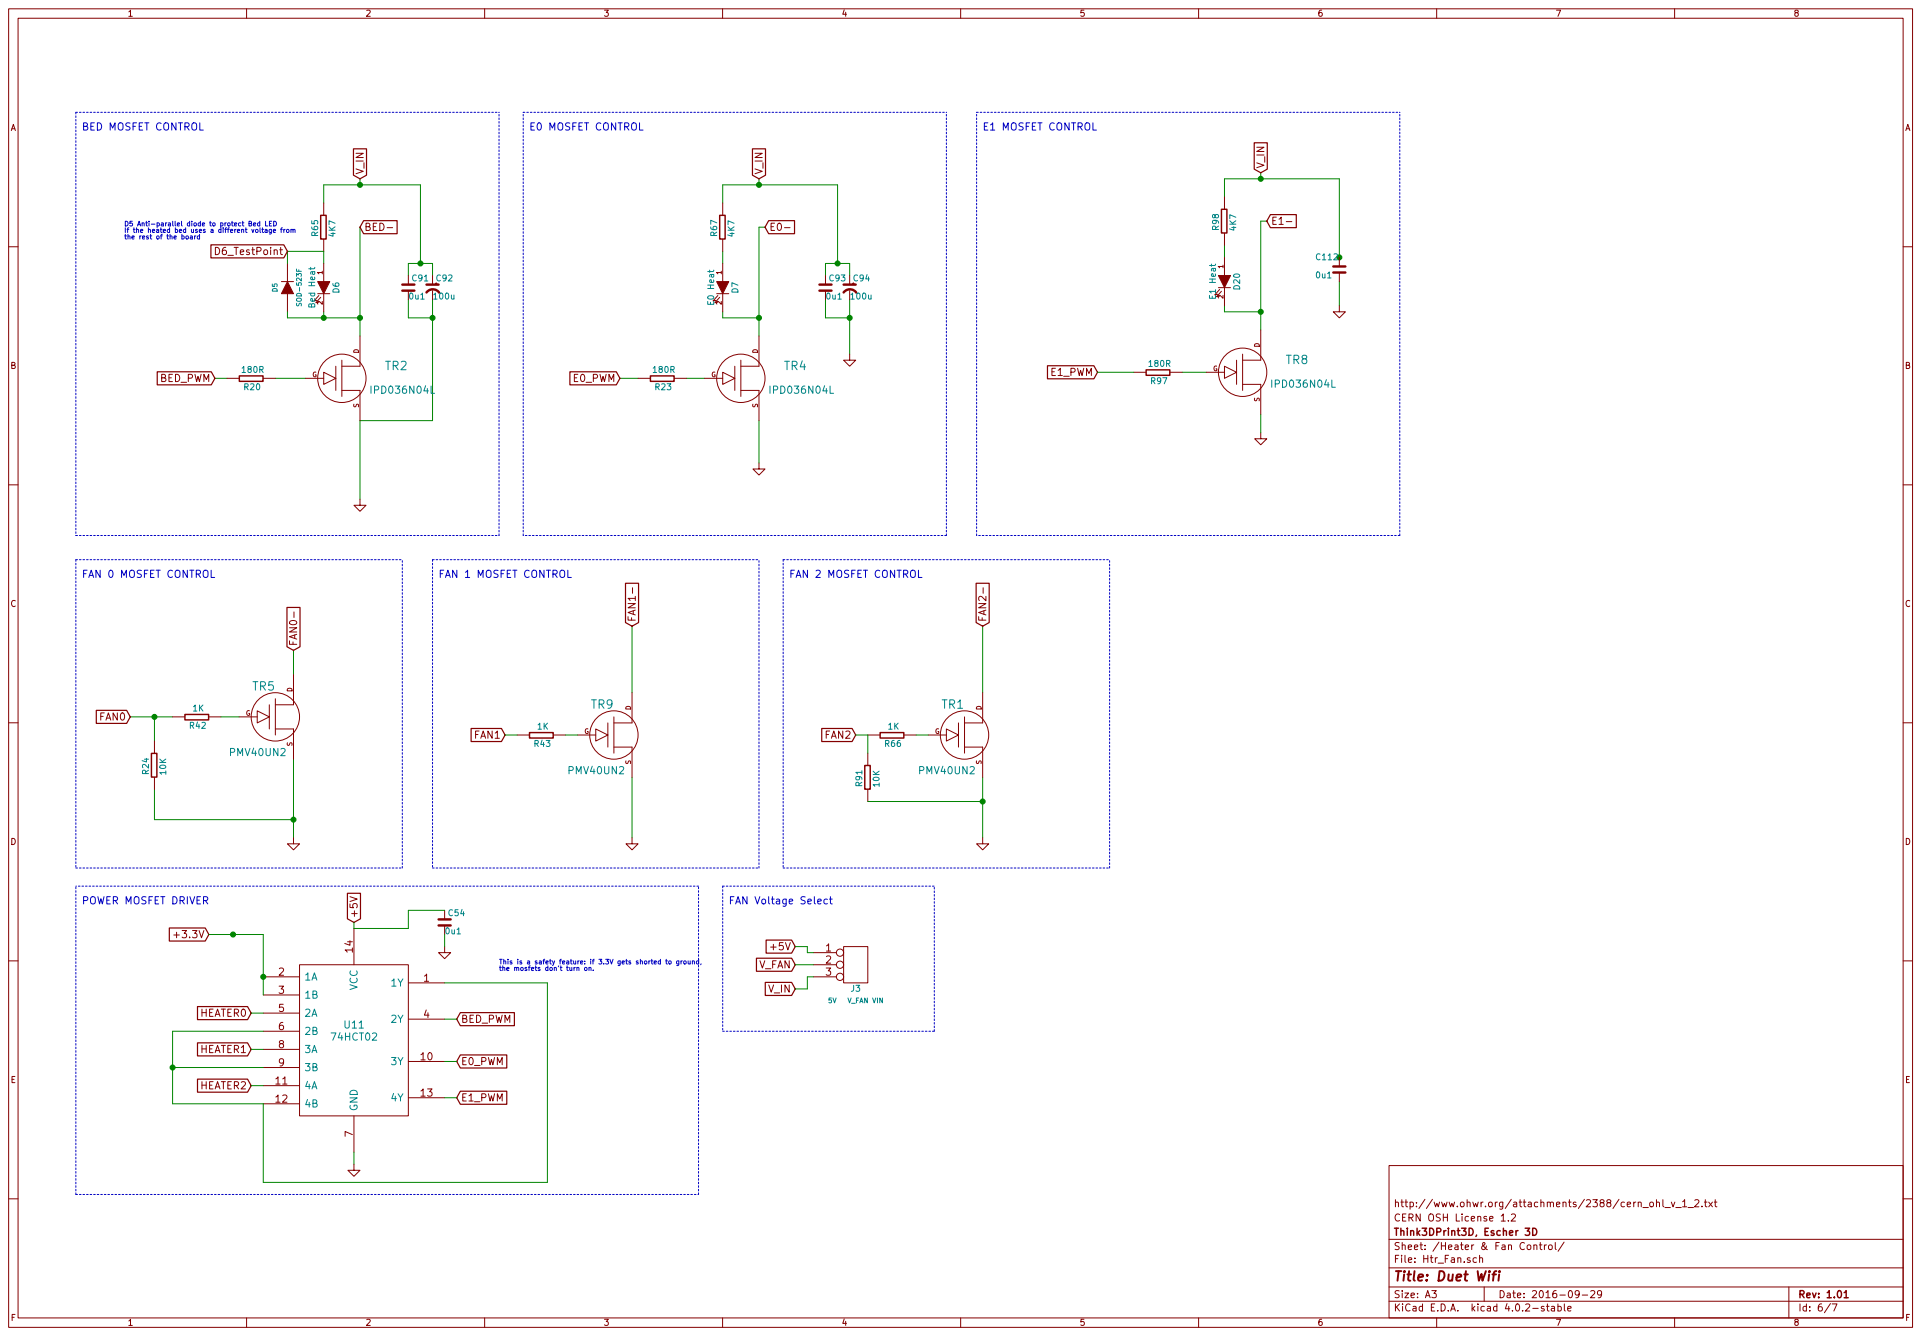
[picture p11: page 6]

If the heated bed uses a different voltage from
the rest of the board

This is a safety feature: if 3.3V gets shorted to ground,
the mosfets don't turn on.

http://www.ohwr.org/attachments/2388/cern_ohl_v_1_2.txt
CERN OSH License 1.2
File: Htr_Fan.sch Sheet: /Heater & Fan Control/ Think3DPrint3D, Escher 3D

Id: 6/7 Title: Duet Wifi

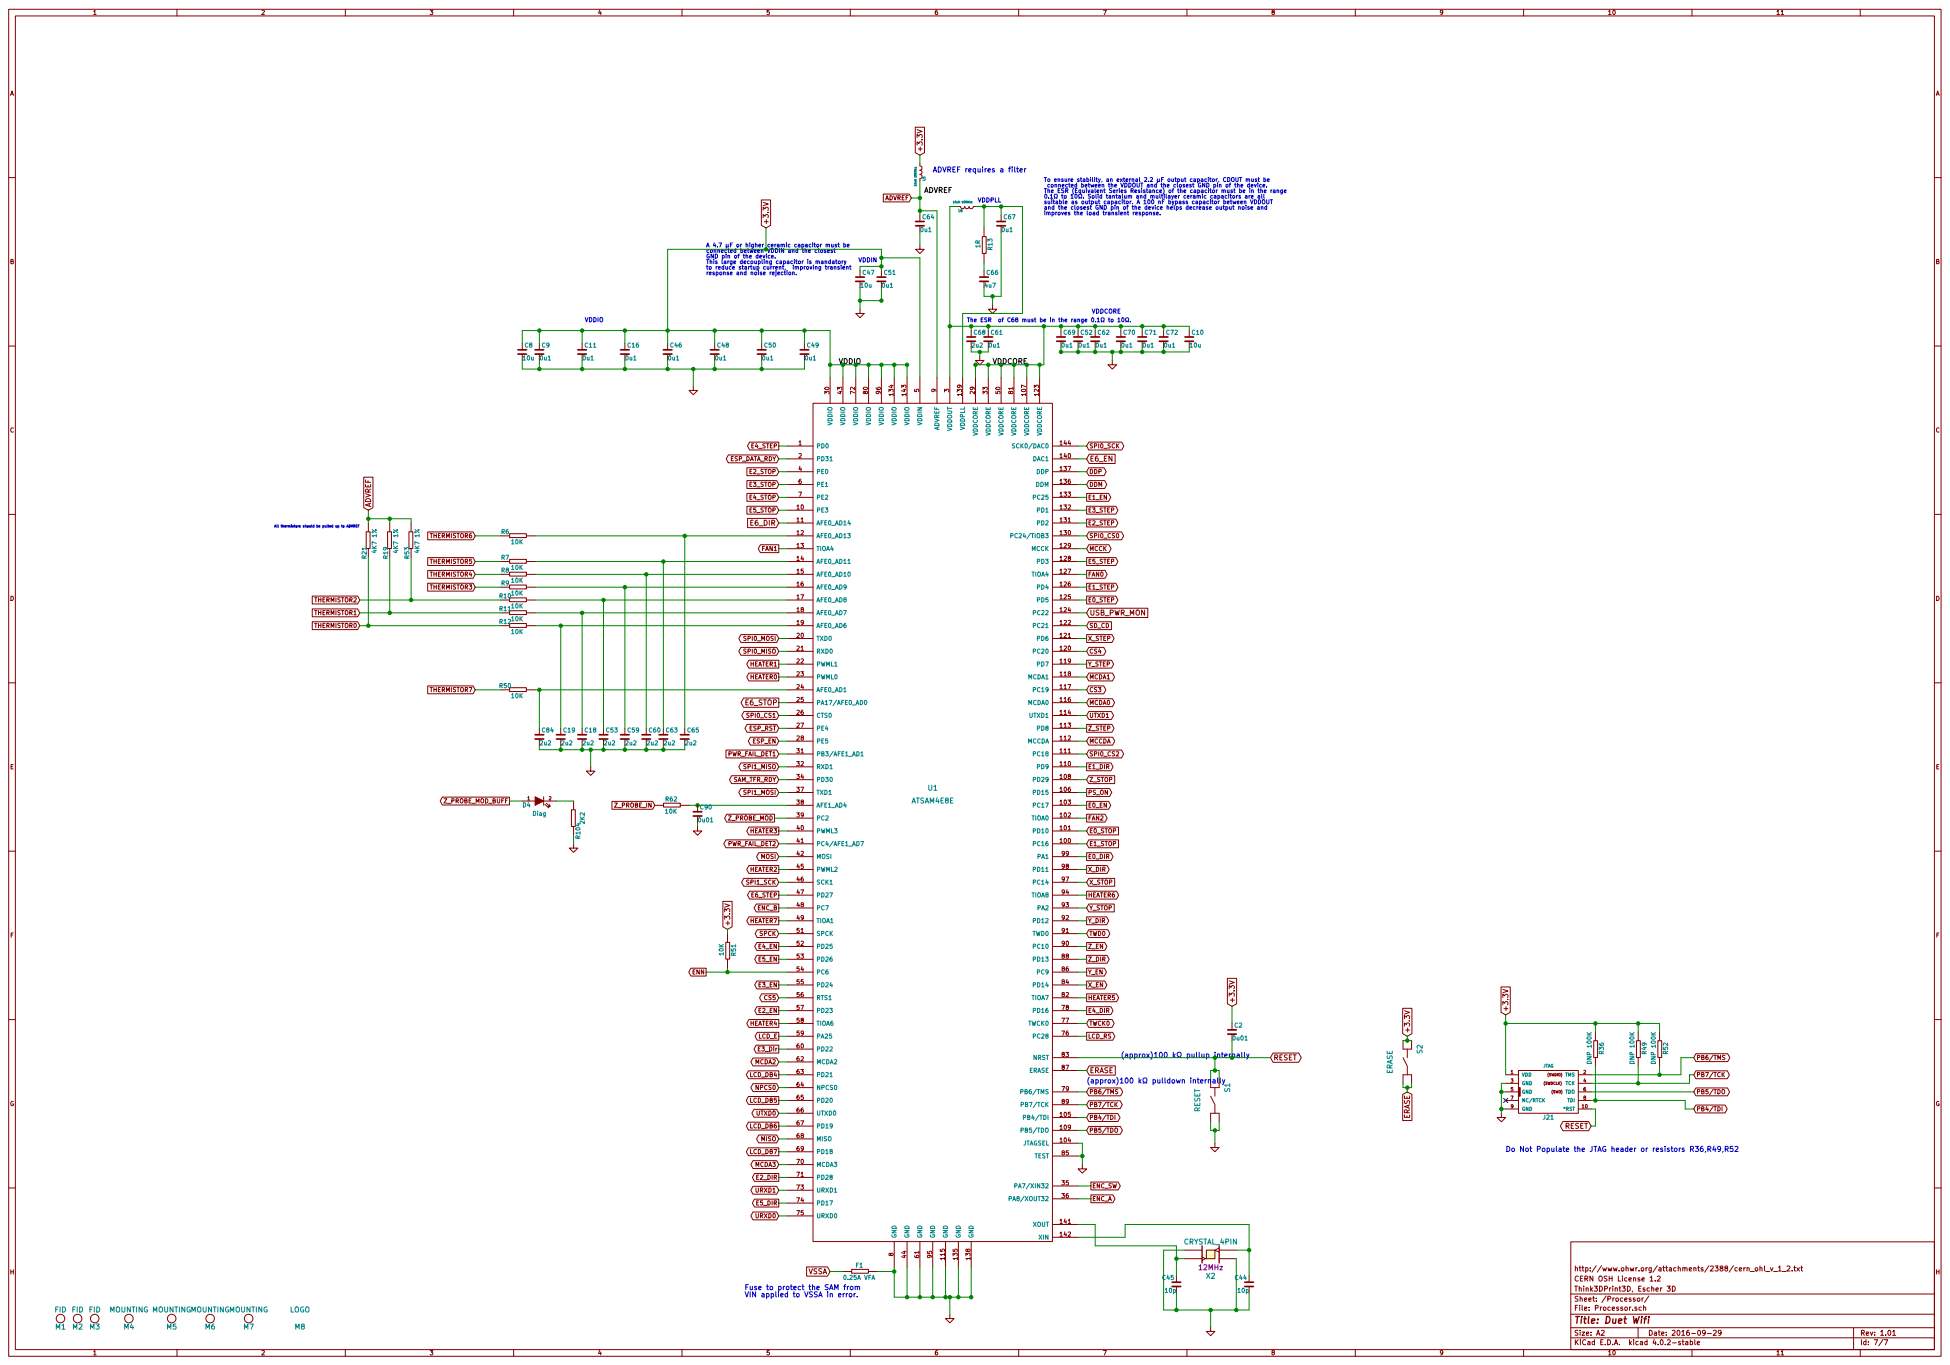
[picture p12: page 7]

connected between the VDDOUT and the closest GND pin of the device. The ESR (Equivalent Series Resistance) of the capacitor must be in the range
0.1 to 10. Solid tantalum and multilayer ceramic capacitors are all suitable as output capacitor. A 100 nF bypass capacitor between VDDOUT
and the closest GND pin of the device helps decrease output noise and

improves the load transient response. C61

A 4.7 F or higher ceramic capacitor must be
connected between VDDIN and the closest GND pin of the device. This large decoupling capacitor is mandatory

(approx)100 k pulldown internally PB6/TMS

Do Not Populate the JTAG header or resistors R36,R49,R52

http://www.ohwr.org/attachments/2388/cern_ohl_v_1_2.txt X2 CRYSTAL_4PIN

CERN OSH License 1.2
Id: 7/7 Title: Duet Wifi File: Processor.sch Sheet: /Processor/ Think3DPrint3D, Escher 3D

0.25A VFA Fuse to protect the SAM from

VIN applied to VSSA in error.

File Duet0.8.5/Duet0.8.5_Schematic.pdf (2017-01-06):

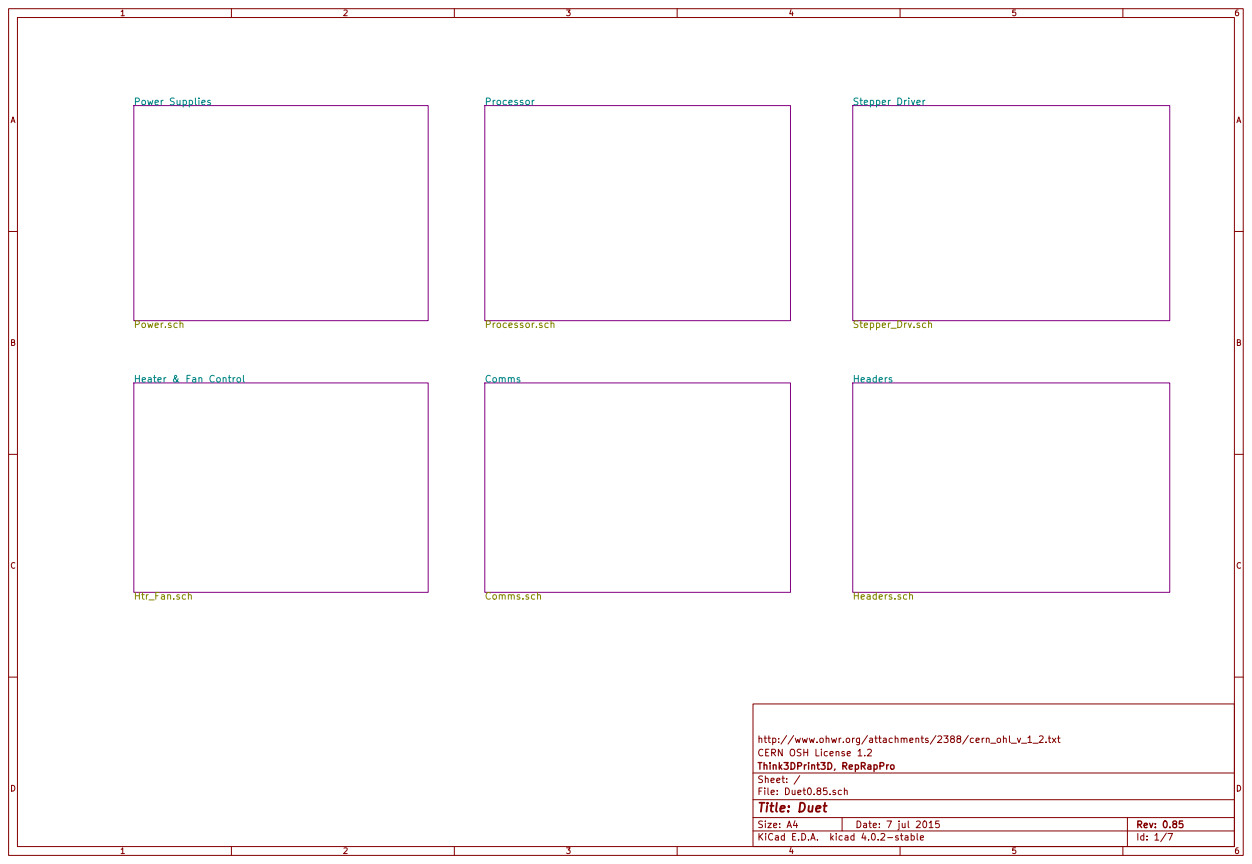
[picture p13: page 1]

http://www.ohwr.org/attachments/2388/cern_ohl_v_1_2.txt
Id: 1/7 Title: Duet File: Duet0.85.sch Sheet: / Think3DPrint3D, RepRapPro CERN OSH License 1.2

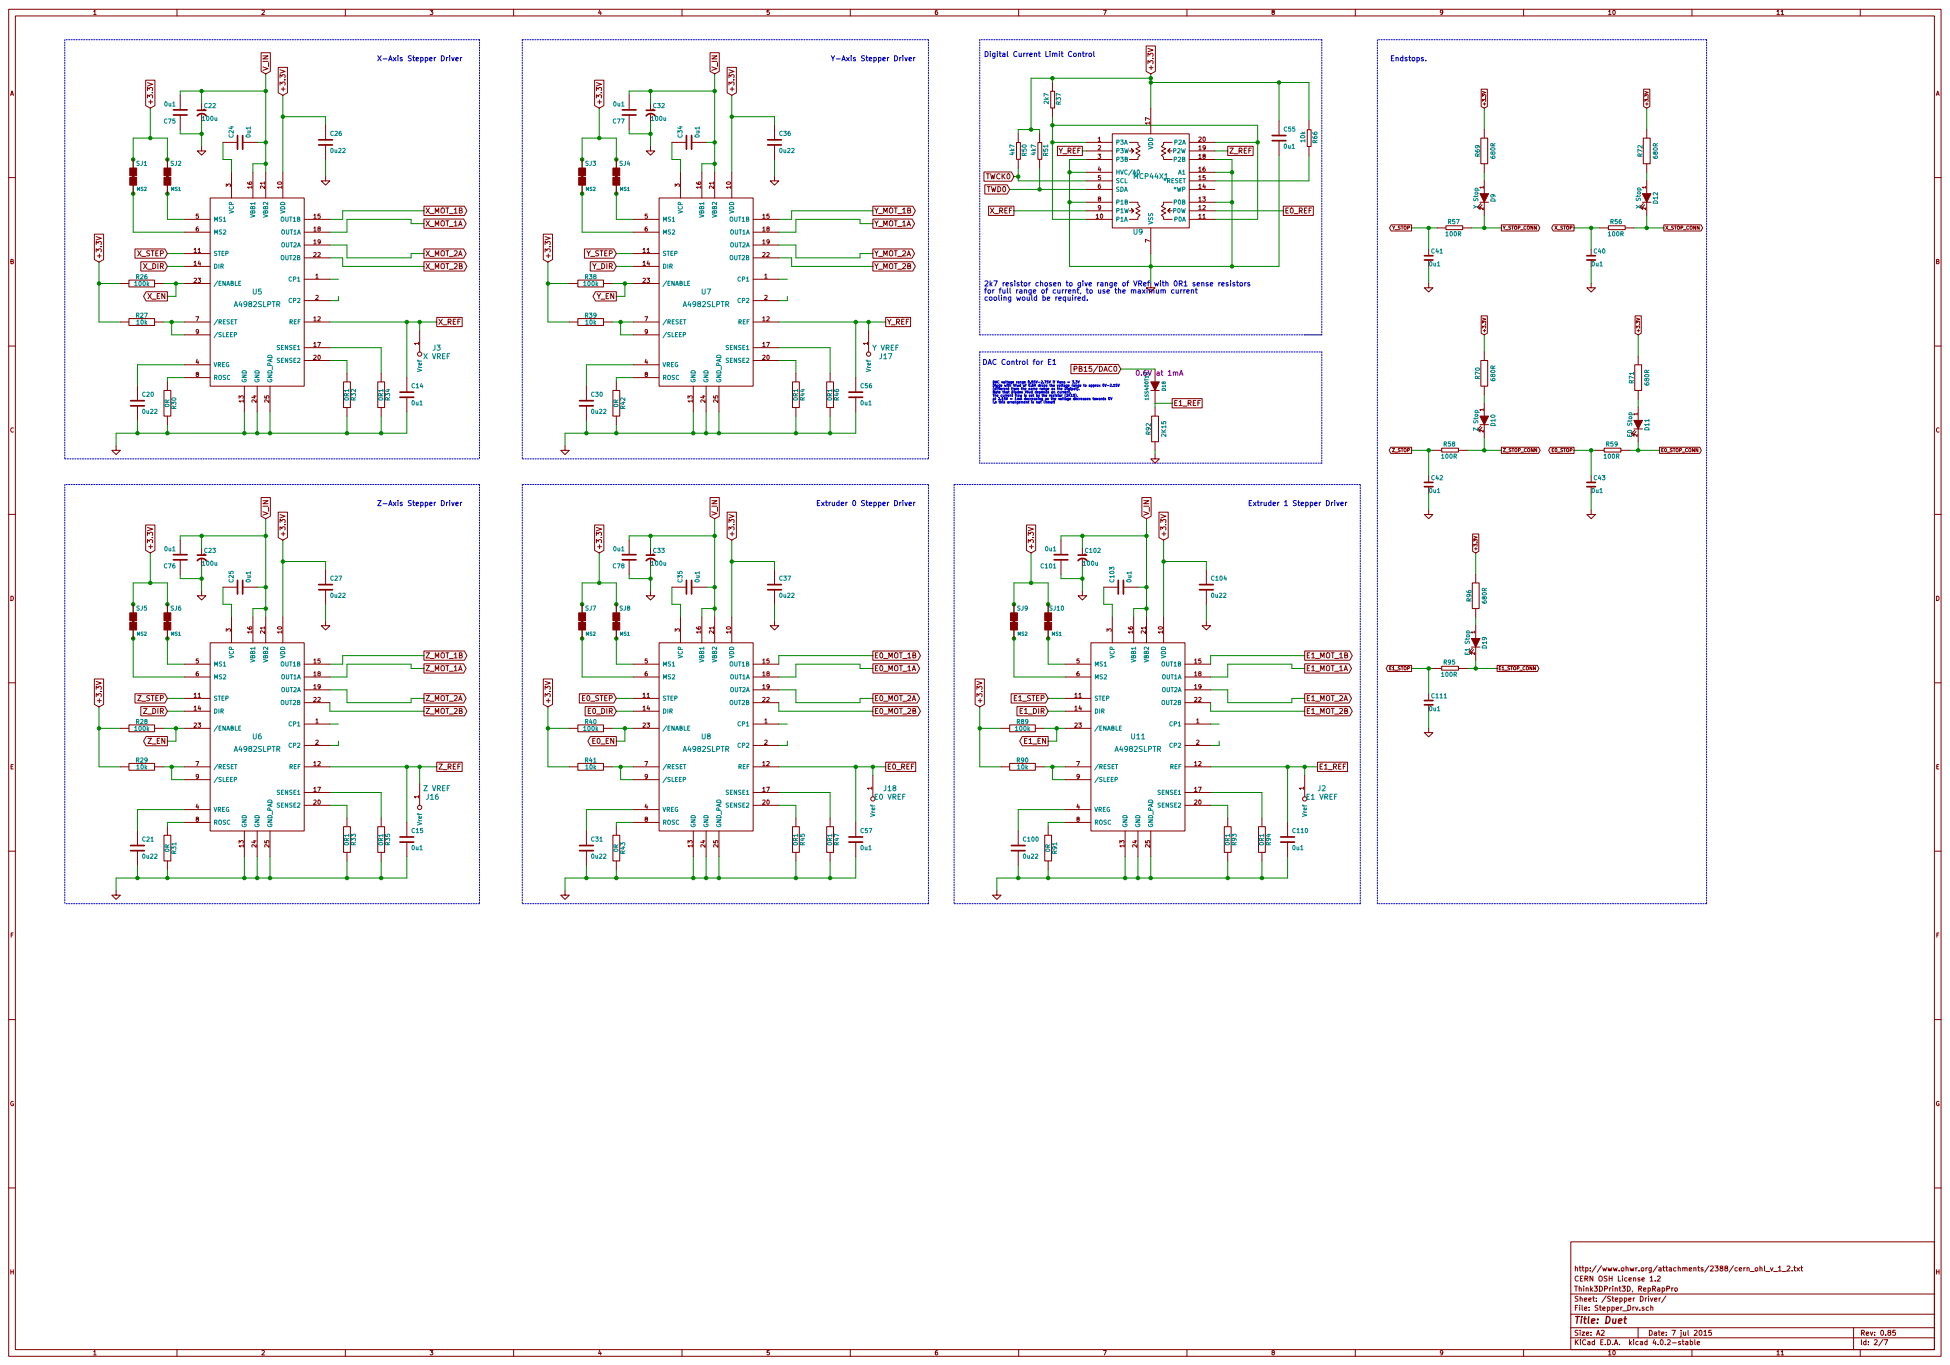
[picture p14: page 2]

Endstops. Digital Current Limit Control

for full range of current, to use the maximum current

DAC voltage range 0.55V-2.75V if Vana = 3.3V Diode with Vfwd of 0.6V drops the voltage range to approx 0V-2.15V
(different from the same range as the Digipot). Note that Diodes Vfwd depends on current. The current flow is set by the resistor (2K15), at 2.15V = 1mA decreasing as the voltage decreases towards 0V

http://www.ohwr.org/attachments/2388/cern_ohl_v_1_2.txt
Think3DPrint3D, RepRapPro CERN OSH License 1.2

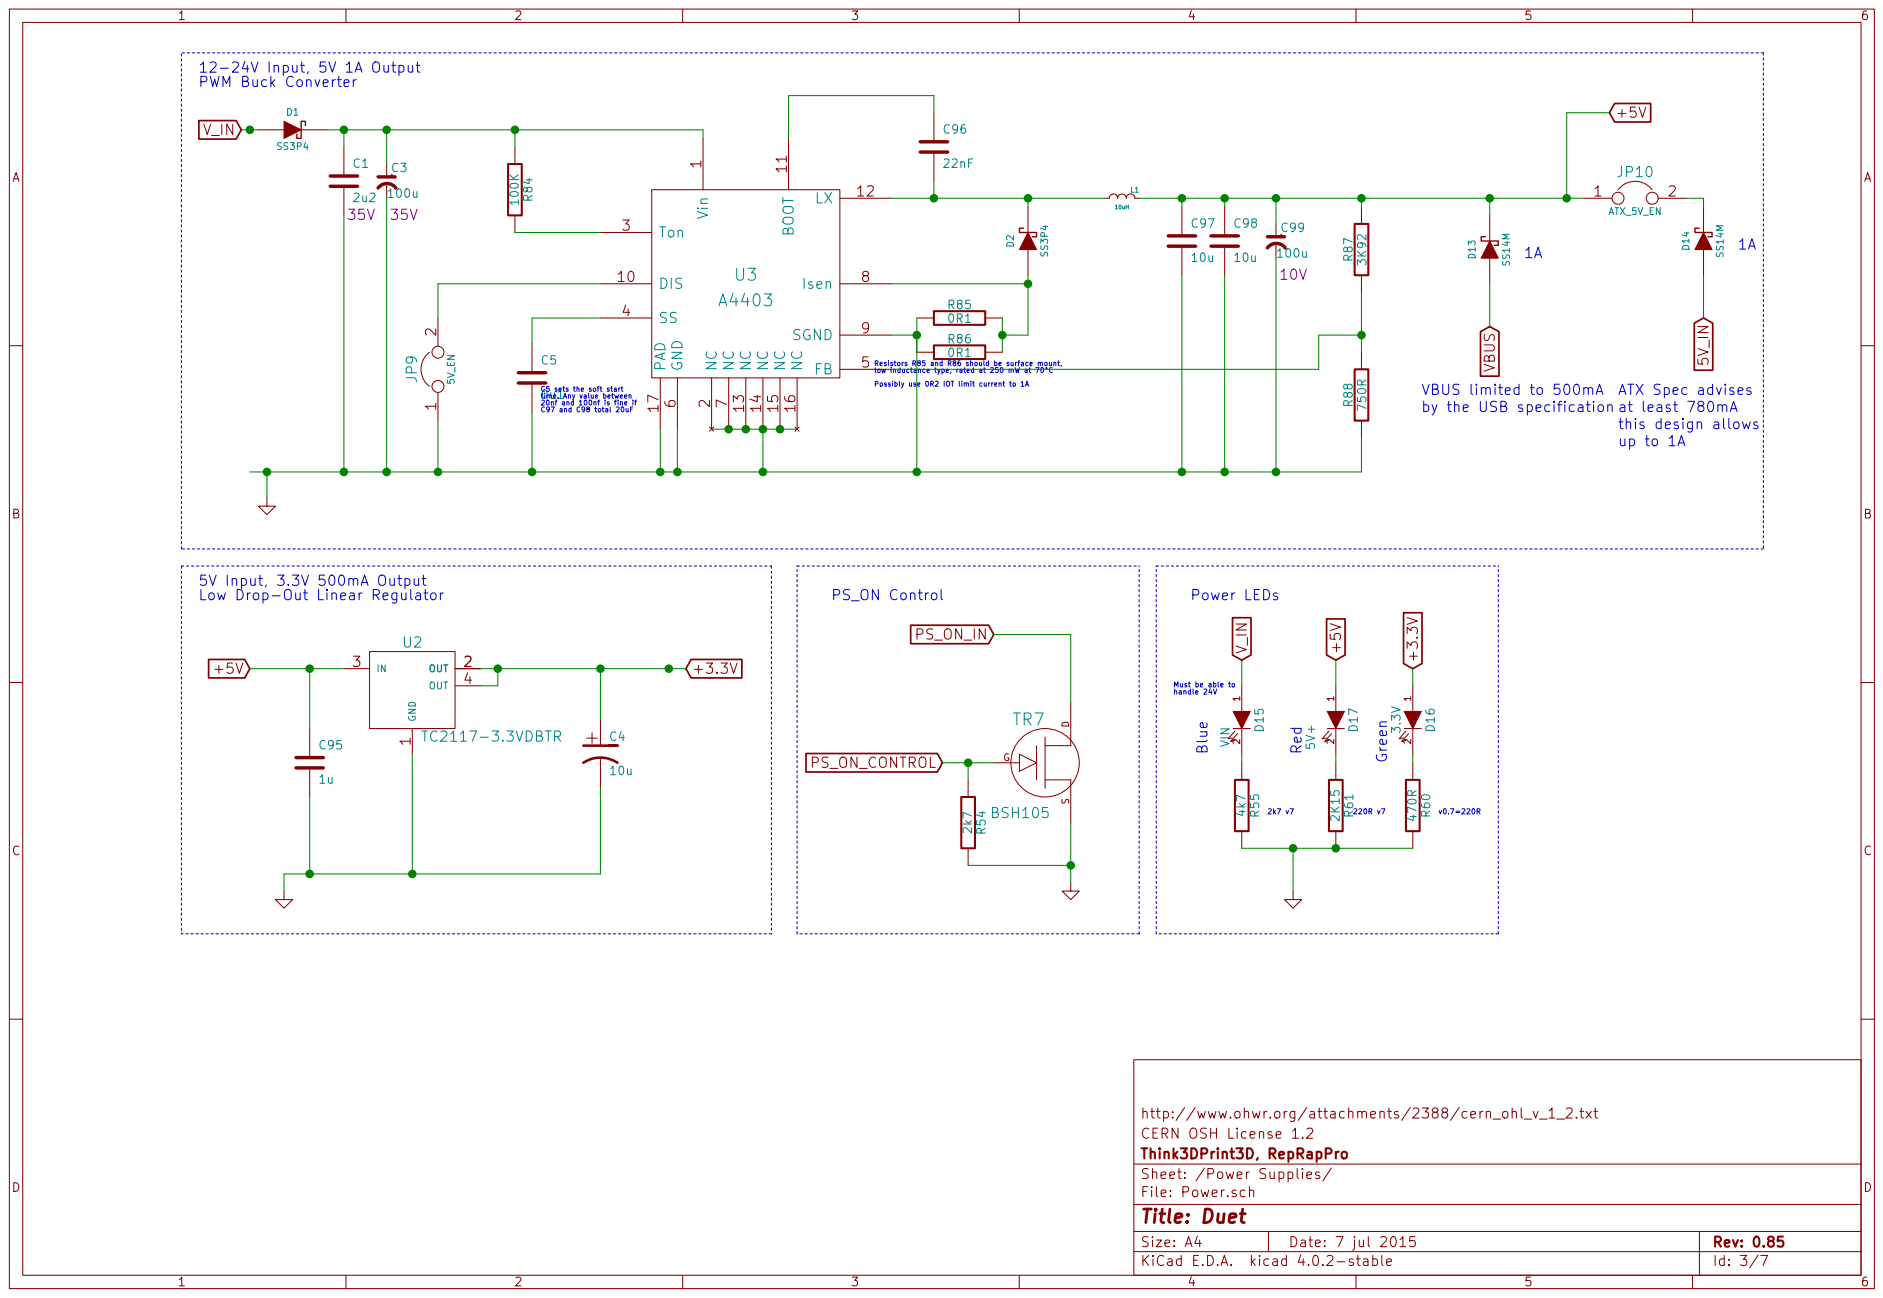
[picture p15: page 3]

U3 A4403 | LX | 12 NC 13 NC 14 NC 15 NC 16 PAD 17

2 Ton 3 SS 4 FB GND 5

Resistors R85 and R86 should be surface mount,
low inductance type, rated at 250 mW at 70°C

Possibly use 0R2 IOT limit current to 1A C5 sets the soft start

time. Any value between

by the USB specification

this design allows at least 780mA

5V Input, 3.3V 500mA Output
Low Drop-Out Linear Regulator

Must be able to

http://www.ohwr.org/attachments/2388/cern_ohl_v_1_2.txt C95

Think3DPrint3D, RepRapPro CERN OSH License 1.2

Id: 3/7 Title: Duet File: Power.sch Sheet: /Power Supplies/

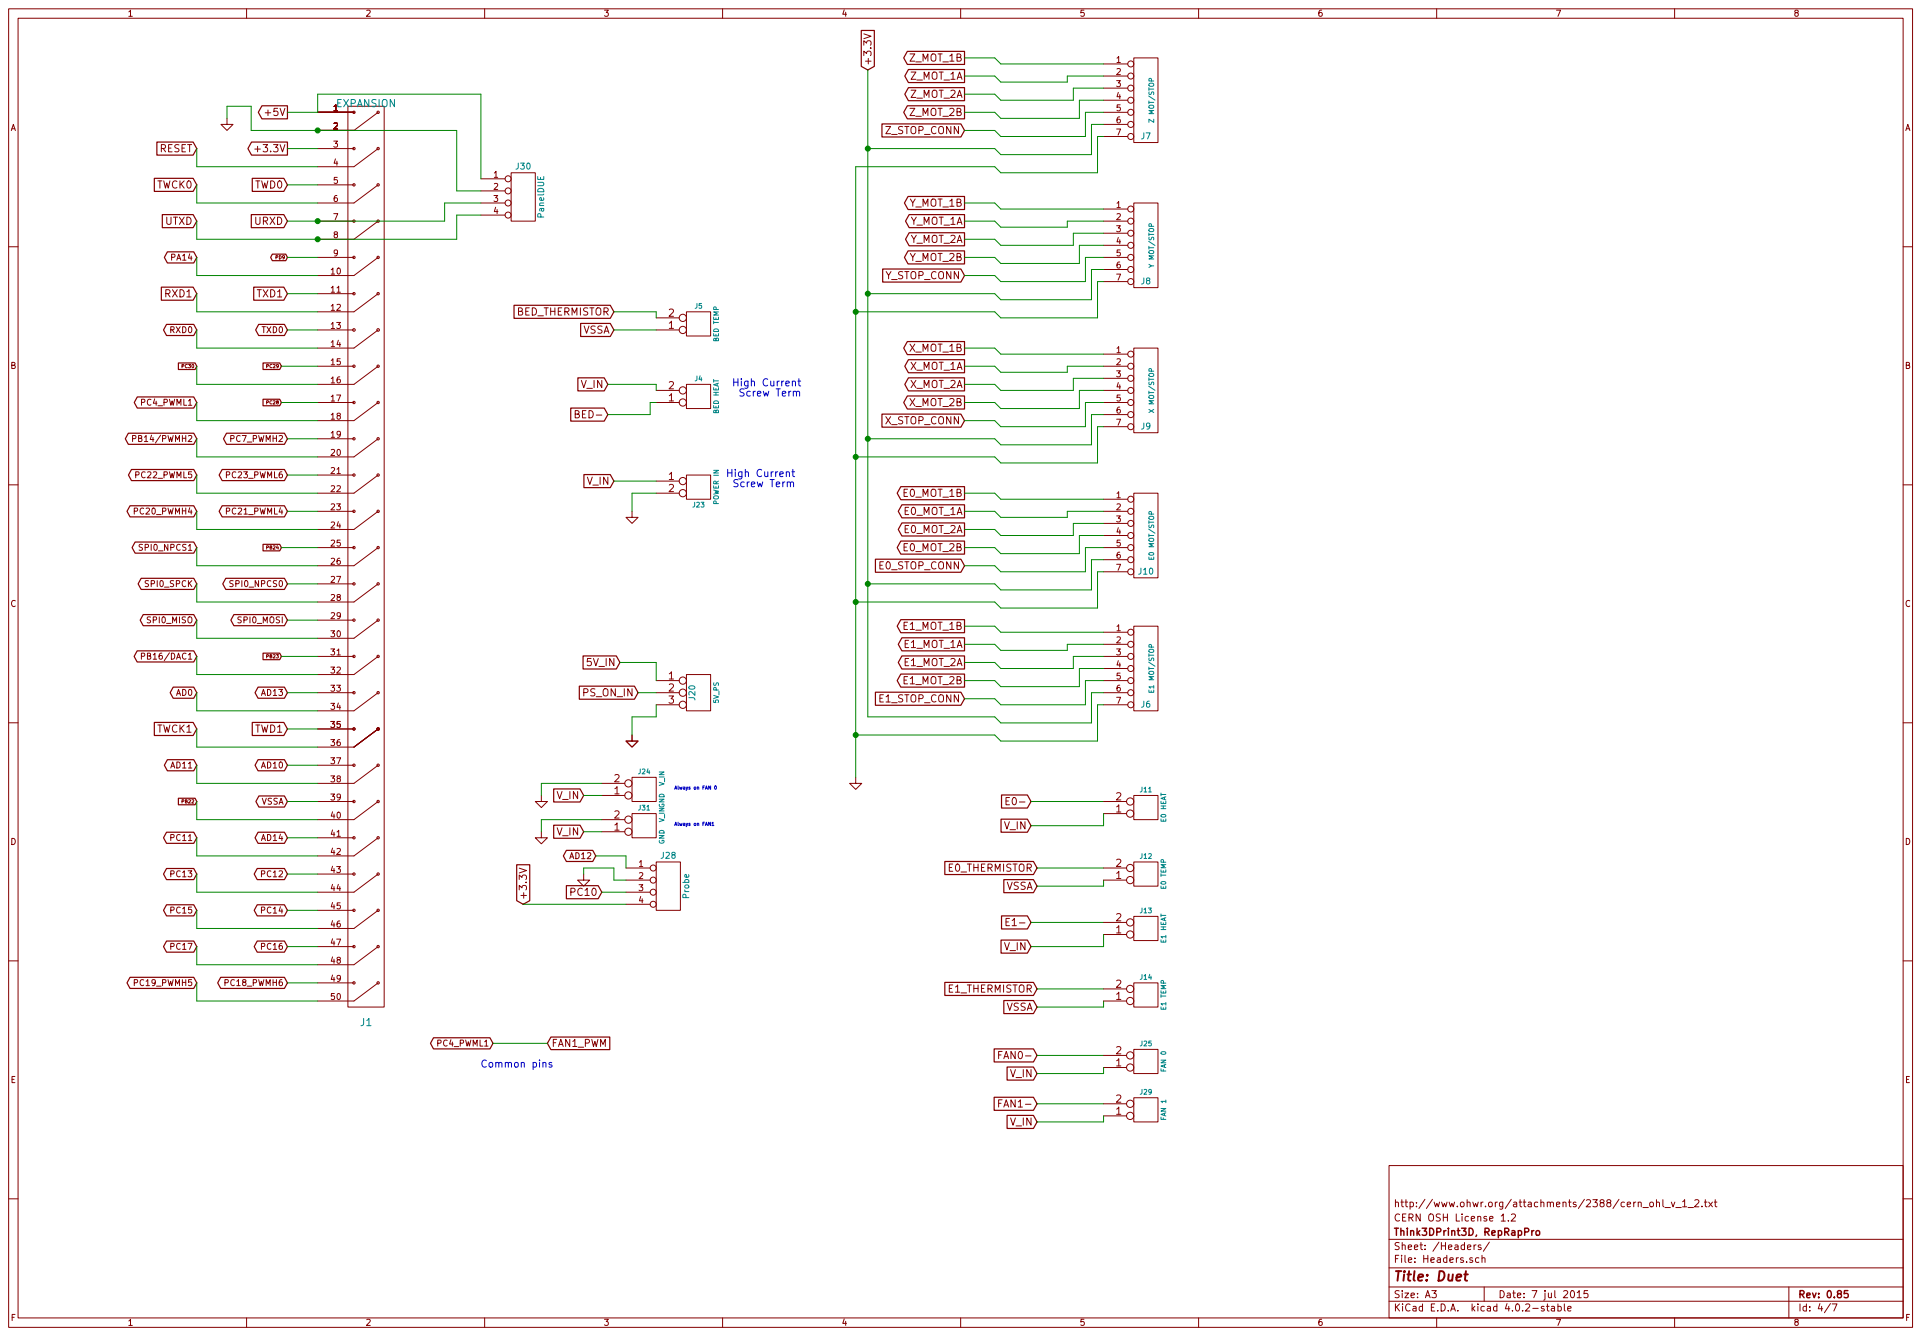
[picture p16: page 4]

Id: 4/7 Title: Duet File: Headers.sch Sheet: /Headers/ Think3DPrint3D, RepRapPro CERN OSH License 1.2


3 RXM 4 RXP 5 TXM 6 TXP 7 X0

XMIT YELLOW | J1 J4

GREEN

Id: 5/7 Title: Duet File: Comms.sch Sheet: /Comms/ Think3DPrint3D, RepRapPro CERN OSH License 1.2


10u +3.3VReturned to 4.7K resistors due to lower noise at
low tempertures causing false open circuit errors

FAN 1 PWM is commoned with E5? PWM on the expansion
connector - If you need
5 extruders you can't have a
second hardware PWM FAN

http://www.ohwr.org/attachments/2388/cern_ohl_v_1_2.txt
File: Htr_Fan.sch Sheet: /Heater & Fan Control/ Think3DPrint3D, RepRapPro CERN OSH License 1.2


http://www.ohwr.org/attachments/2388/cern_ohl_v_1_2.txt R81

Id: 7/7 Title: Duet File: Processor.sch Sheet: /Processor/ Think3DPrint3D, RepRapPro CERN OSH License 1.2

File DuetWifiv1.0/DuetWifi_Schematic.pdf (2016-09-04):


http://www.ohwr.org/attachments/2388/cern_ohl_v_1_2.txt
CERN OSH License 1.2
Id: 1/7 Title: Duet Wifi File: DuetWifi.sch Sheet: / Think3DPrint3D, Escher 3D


Y-Axis Stepper Driver X-Axis Stepper Driver

Stepper circuit EMI protection

http://www.ohwr.org/attachments/2388/cern_ohl_v_1_2.txt
CERN OSH License 1.2
Think3DPrint3D, Escher 3D
Sheet: /Stepper Driver/
File: Stepper_Drv.sch
Id: 2/7 Title: Duet Wifi


U3 A4403 | LX | 12 NC 13 NC 14 NC 15 NC 16 PAD 17

2 Ton 3 SS 4 FB GND 5

Possibly use 0R2 IOT limit current to 1A C5 sets the soft start

time. Any value between

Resistors R85 and R86 should be surface mount,
low inductance type, rated at 250 mW at 70°C

by the USB specification

this design allows at least 780mA

5V Input, 3.3V 500mA Output
Low Drop-Out Linear Regulator

Must be able to

http://www.ohwr.org/attachments/2388/cern_ohl_v_1_2.txt
CERN OSH License 1.2
Think3DPrint3D, Escher 3D
Id: 3/7 Title: Duet Wifi File: Power.sch Sheet: /Power Supplies/


J39 Not populated in production boards

CERN OSH License 1.2
Id: 4/7 Title: Duet Wifi File: Headers.sch Sheet: /Headers/ Think3DPrint3D, Escher 3D


Do not populate C17 unless
the layout changes moving

CERN OSH License 1.2
Id: 5/7 Title: Duet Wifi File: Comms.sch Sheet: /Comms/ Think3DPrint3D, Escher 3D


If the heated bed uses a different voltage from
the rest of the board

This is a safety feature: if 3.3V gets shorted to ground,
the mosfets don't turn on.

http://www.ohwr.org/attachments/2388/cern_ohl_v_1_2.txt
CERN OSH License 1.2
File: Htr_Fan.sch Sheet: /Heater & Fan Control/ Think3DPrint3D, Escher 3D

Id: 6/7 Title: Duet Wifi


connected between the VDDOUT and the closest GND pin of the device. The ESR (Equivalent Series Resistance) of the capacitor must be in the range
0.1 to 10. Solid tantalum and multilayer ceramic capacitors are all suitable as output capacitor. A 100 nF bypass capacitor between VDDOUT
and the closest GND pin of the device helps decrease output noise and

improves the load transient response. C61

A 4.7 F or higher ceramic capacitor must be
connected between VDDIN and the closest GND pin of the device. This large decoupling capacitor is mandatory

(approx)100 k pulldown internally PB6/TMS

Do Not Populate the JTAG header or resistors R36,R49,R52

http://www.ohwr.org/attachments/2388/cern_ohl_v_1_2.txt
CERN OSH License 1.2
Id: 7/7 Title: Duet Wifi File: Processor.sch Sheet: /Processor/ Think3DPrint3D, Escher 3D

0.25A VFA Fuse to protect the SAM from

VIN applied to VSSA in error.

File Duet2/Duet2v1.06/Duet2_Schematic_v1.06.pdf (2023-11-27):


https://github.com/T3P3/Duet/blob/master/LICENSE
File: Duet2.kicad_sch Sheet: / Duet3D


9 U4 ESP-WROOM-02 VBUS 1 DN 2 DP 3

https://github.com/T3P3/Duet/blob/master/LICENSE
File: Comms.kicad_sch Sheet: /Comms/ Duet3D


File: Headers.kicad_sch Sheet: /Headers/ Duet3D


FAN Voltage Select & Fuse

Extruder Heater/Stepper/5V supply Fuse

https://github.com/T3P3/Duet/blob/master/LICENSE
File: Htr_Fan.kicad_sch Sheet: /Heater & Fan Control/ Duet3D


Must be able to
handle 24V

https://github.com/T3P3/Duet/blob/master/LICENSE
Sheet: /Power Supplies/ Duet3D


All thermistors should be pulled up to ADVREF

https://github.com/T3P3/Duet/blob/master/LICENSE
File: Processor.kicad_sch Sheet: /Processor/ Duet3D


4 VCC_IO 40 DIR 41 STEP 42 TST_MODE 43 GND 44 OA2 5.6 OA1 7.8 BRA 9 U5 TMC2660 C24 0u1 X7R 10% 50V C20 0u47 X5R 10%, 10V

4 VCC_IO 40 DIR 41 STEP 42 TST_MODE 43 GND 44 OA2 5.6 OA1 7.8 BRA 9 U7 TMC2660 C31 0u47 X5R 10%, 10V R69 1K

Extruder 1 Stepper Driver C30 between pin 13 and 17

4 VCC_IO 40 DIR 41 STEP 42 TST_MODE 43 GND 44 OA2 5.6 OA1 7.8 BRA 9 U8 TMC2660 R40 22R

4 VCC_IO 40 DIR 41 STEP 42 TST_MODE 43 GND 44 OA2 5.6 OA1 7.8 BRA 9 U9 TMC2660

https://github.com/T3P3/Duet/blob/master/LICENSE
Sheet: /Stepper Driver/ Duet3D

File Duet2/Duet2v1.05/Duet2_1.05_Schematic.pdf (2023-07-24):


Sheet: Processor File: Processor.sch

Sheet: Heater & Fan Control

https://github.com/T3P3/Duet/blob/master/LICENSE
File: Duet2.sch Sheet: / Duet3D


https://github.com/T3P3/Duet/blob/master/LICENSE
Sheet: /Stepper Driver/ Duet3D


2 Ton 3 SS 4 FB GND 5

C5 sets the soft start
time. Any value between

5V Input, 3.3V 500mA Output
Low Drop-Out Linear Regulator

Must be able to

U2 is close enough to
C7 that a seperate
decoupling cap
is not required

https://github.com/T3P3/Duet/blob/master/LICENSE
File: Power.sch Sheet: /Power Supplies/ Duet3D


All test points are DNP

File: Headers.sch Sheet: /Headers/ Duet3D


https://github.com/T3P3/Duet/blob/master/LICENSE
File: Comms.sch Sheet: /Comms/ Duet3D


BED- FAN 0 MOSFET CONTROL

D5 Anti-parallel diode to protect Bed LED
If the heated bed uses a different voltage from

the mosfets don't turn on. POWER MOSFET DRIVER

FAN Voltage Select & Fuse

This is a safety feature: if 3.3V gets shorted to ground,

Extruder Heater/Stepper/5V supply Fuse

https://github.com/T3P3/Duet/blob/master/LICENSE
File: Htr_Fan.sch Sheet: /Heater & Fan Control/ Duet3D


connected between the VDDOUT and the closest GND pin of the device. The ESR (Equivalent Series Resistance) of the capacitor must be in the range

0.1 to 10. Solid tantalum and multilayer ceramic capacitors are all suitable as output capacitor. A 100 nF bypass capacitor between VDDOUT

improves the load transient response. The ESR of C68 must be in the range 0.1 to 10.

and the closest GND pin of the device helps decrease output noise and

A 4.7 F or higher ceramic capacitor must be
connected between VDDIN and the closest GND pin of the device. This large decoupling capacitor is mandatory

All thermistors should be pulled up to ADVREF

https://github.com/T3P3/Duet/blob/master/LICENSE M4 MOUNTING

Fuse to protect the SAM from
VIN applied to VSSA in error.

File: Processor.sch Sheet: /Processor/ Duet3D

M10 CE Logo M9 CE Logo

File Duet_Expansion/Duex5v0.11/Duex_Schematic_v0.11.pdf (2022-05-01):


Sheet: Headers & Power File: Headers.sch Sheet: Heater & Fan Control

https://github.com/duet3d/hardware
Duet3D license (based on CERN OSH License 1.2)
File: Duex5.sch Sheet: / Duet3D


4 VCC_IO 40 DIR 41 STEP 42 TST_MODE 43 GND 44 OA2 5.6 OA1 7.8 BRA 9 U1 TMC2660 C9

4 VCC_IO 40 DIR 41 STEP 42 TST_MODE 43 GND 44 OA2 5.6 OA1 7.8 BRA 9 U2 TMC2660 R9 0R050 R17 0R050 R6 22R

4 VCC_IO 40 DIR 41 STEP 42 TST_MODE 43 GND 44 OA2 5.6 OA1 7.8 BRA 9 U5 TMC2660 R77 10K R76 R80 10K R4 10K 10K C38 1n >50VC57 1n >50VC65 1n >50V

V0.11: R82: DNP R83: DNP R84: DNP R85: DNP R86: 10K

4 VCC_IO 40 DIR 41 STEP 42 TST_MODE 43 GND 44 OA2 5.6 OA1 7.8 BRA 9 U6 TMC2660

Duet3D license (based on CERN OSH License 1.2)
Sheet: /Stepper Driver/ Duet3D


Commoned with heater PWM

https://github.com/duet3d/hardware 123

Duet3D license (based on CERN OSH License 1.2)
File: Headers.sch Sheet: /Headers & Power/ Duet3D


Always populate R67, even on Duex2

2bit Board ID
in conjunction with I/O[15] R66 is DNP on Duex2

https://github.com/duet3d/hardware
Duet3D license (based on CERN OSH License 1.2)
File: Htr_Fan.sch Sheet: /Heater & Fan Control/ Duet3D

This is a safety feature: if 3.3V gets shorted to ground,
the mosfets don't turn on.

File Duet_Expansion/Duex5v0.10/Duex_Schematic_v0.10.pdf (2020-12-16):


Sheet: Headers & Power File: Headers.sch Sheet: Heater & Fan Control

https://github.com/duet3d/hardware
Duet3D license (based on CERN OSH License 1.2)
File: Duex5.sch Sheet: / Duet3D


4 VCC_IO 40 DIR 41 STEP 42 TST_MODE 43 GND 44 OA2 5.6 OA1 7.8 BRA 9 U2 TMC2660 C1

4 VCC_IO 40 DIR 41 STEP 42 TST_MODE 43 GND 44 OA2 5.6 OA1 7.8 BRA 9 U1 TMC2660

4 VCC_IO 40 DIR 41 STEP 42 TST_MODE 43 GND 44 OA2 5.6 OA1 7.8 BRA 9 U5 TMC2660 C57 1n >50VC65 1n >50VC66 1n >50V C24 1n >50VC25 1n >50V C33

4 VCC_IO 40 DIR 41 STEP 42 TST_MODE 43 GND 44 OA2 5.6 OA1 7.8 BRA 9 U6 TMC2660

Duet3D license (based on CERN OSH License 1.2)
Sheet: /Stepper Driver/ Duet3D


Input header (expansion on DuexWifi)

All test points are DNP

The E2-E5 test points
are not required for ATE
however they do
provide a point for
users to add stp/dir/en

headers for external drivers Port Expander IO

Servos/PWM
Commoned with heater PWM

Duet3D license (based on CERN OSH License 1.2)
File: Headers.sch Sheet: /Headers & Power/ Duet3D


in conjunction with I/O[15] R66 is DNP on Duex2

https://github.com/duet3d/hardware
Duet3D license (based on CERN OSH License 1.2)
File: Htr_Fan.sch Sheet: /Heater & Fan Control/ Duet3D

This is a safety feature: if 3.3V gets shorted to ground,
the mosfets don't turn on.

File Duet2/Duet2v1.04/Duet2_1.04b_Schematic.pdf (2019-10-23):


https://github.com/T3P3/Duet/blob/master/LICENSE
File: Duet2.sch Sheet: / Think3DPrint3D, Escher 3D


Y-Axis Stepper Driver X-Axis Stepper Driver

https://github.com/T3P3/Duet/blob/master/LICENSE
Think3DPrint3D, Escher 3D
Sheet: /Stepper Driver/
File: Stepper_Drv.sch
Id: 2/7 Title: Duet 2


2 Ton 3 SS 4 FB GND 5

by the USB specification

this design allows at least 780mA

C5 sets the soft start
time. Any value between

5V Input, 3.3V 500mA Output
Low Drop-Out Linear Regulator

Must be able to

U2 is close enough to
C7 that a seperate
decoupling cap
is not required

https://github.com/T3P3/Duet/blob/master/LICENSE
Think3DPrint3D, Escher 3D
File: Power.sch Sheet: /Power Supplies/
Id: 3/7 Title: Duet 2


File: Headers.sch Sheet: /Headers/ Think3DPrint3D, Escher 3D


C92 is on the bottom of the board. ESP_3.3VIN

File: Comms.sch Sheet: /Comms/ Think3DPrint3D, Escher 3D


If the heated bed uses a different voltage from
the rest of the board

FAN Voltage Select & Fuse

This is a safety feature: if 3.3V gets shorted to ground,
the mosfets don't turn on.

Extruder Heater/Stepper/5V supply Fuse

https://github.com/T3P3/Duet/blob/master/LICENSE
File: Htr_Fan.sch Sheet: /Heater & Fan Control/ Think3DPrint3D, Escher 3D


connected between the VDDOUT and the closest GND pin of the device. The ESR (Equivalent Series Resistance) of the capacitor must be in the range
0.1 to 10. Solid tantalum and multilayer ceramic capacitors are all suitable as output capacitor. A 100 nF bypass capacitor between VDDOUT
and the closest GND pin of the device helps decrease output noise and

improves the load transient response. C61

A 4.7 F or higher ceramic capacitor must be
connected between VDDIN and the closest GND pin of the device. This large decoupling capacitor is mandatory

https://github.com/T3P3/Duet/blob/master/LICENSE X2 CRYSTAL_4PIN

F1 PPTC Resettable Fuse Fuse to protect the SAM from

File: Processor.sch Sheet: /Processor/ Think3DPrint3D, Escher 3D

VIN applied to VSSA in error.
Multicomp MC36207, Bel Fuse 0ZCJ0020FF2E

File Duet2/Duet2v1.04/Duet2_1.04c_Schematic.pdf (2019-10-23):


https://github.com/T3P3/Duet/blob/master/LICENSE
File: Duet2.sch Sheet: / Duet3D


Y-Axis Stepper Driver X-Axis Stepper Driver

https://github.com/T3P3/Duet/blob/master/LICENSE
Sheet: /Stepper Driver/ Duet3D


2 Ton 3 SS 4 FB GND 5

by the USB specification

this design allows at least 780mA

C5 sets the soft start
time. Any value between

5V Input, 3.3V 500mA Output
Low Drop-Out Linear Regulator

Must be able to

U2 is close enough to
C7 that a seperate
decoupling cap
is not required

https://github.com/T3P3/Duet/blob/master/LICENSE
File: Power.sch Sheet: /Power Supplies/ Duet3D


File: Headers.sch Sheet: /Headers/ Duet3D


C92 is on the bottom of the board. ESP_3.3VIN

File: Comms.sch Sheet: /Comms/ Duet3D


If the heated bed uses a different voltage from
the rest of the board

FAN Voltage Select & Fuse

This is a safety feature: if 3.3V gets shorted to ground,
the mosfets don't turn on.

Extruder Heater/Stepper/5V supply Fuse

https://github.com/T3P3/Duet/blob/master/LICENSE
File: Htr_Fan.sch Sheet: /Heater & Fan Control/ Duet3D


connected between the VDDOUT and the closest GND pin of the device. The ESR (Equivalent Series Resistance) of the capacitor must be in the range
0.1 to 10. Solid tantalum and multilayer ceramic capacitors are all suitable as output capacitor. A 100 nF bypass capacitor between VDDOUT
and the closest GND pin of the device helps decrease output noise and

improves the load transient response. C61

A 4.7 F or higher ceramic capacitor must be
connected between VDDIN and the closest GND pin of the device. This large decoupling capacitor is mandatory

https://github.com/T3P3/Duet/blob/master/LICENSE X2 CRYSTAL_4PIN

F1 PPTC Resettable Fuse Fuse to protect the SAM from

File: Processor.sch Sheet: /Processor/ Duet3D

VIN applied to VSSA in error.
Multicomp MC36207, Bel Fuse 0ZCJ0020FF2E








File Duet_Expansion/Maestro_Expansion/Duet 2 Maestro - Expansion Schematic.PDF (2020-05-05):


1 | E2_MOT_1B

1 | | | E3_MOT_1B
CLK 27 | 9



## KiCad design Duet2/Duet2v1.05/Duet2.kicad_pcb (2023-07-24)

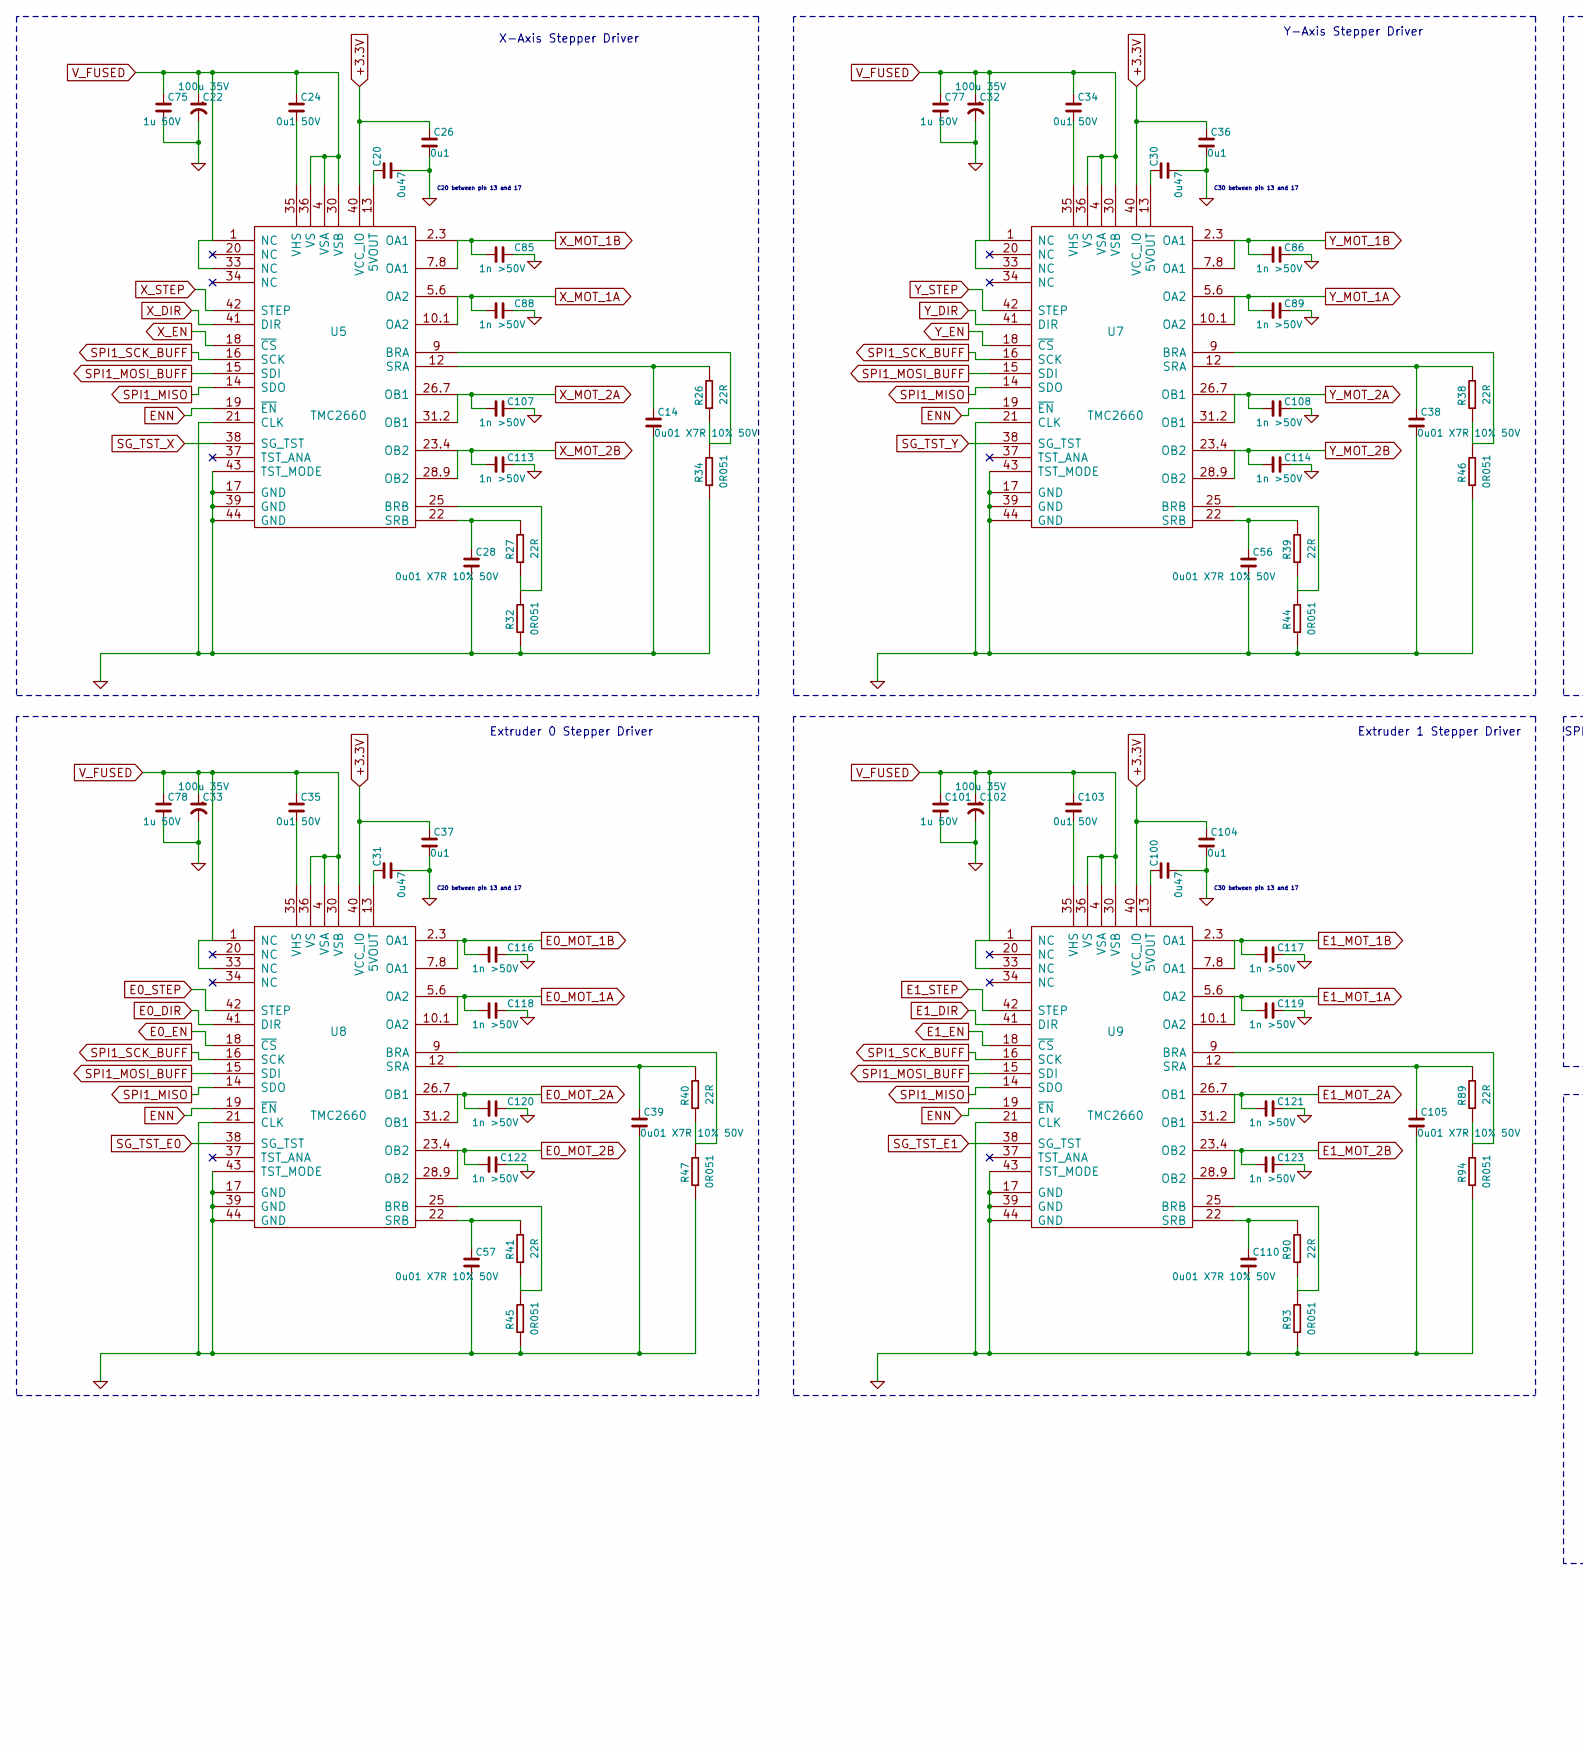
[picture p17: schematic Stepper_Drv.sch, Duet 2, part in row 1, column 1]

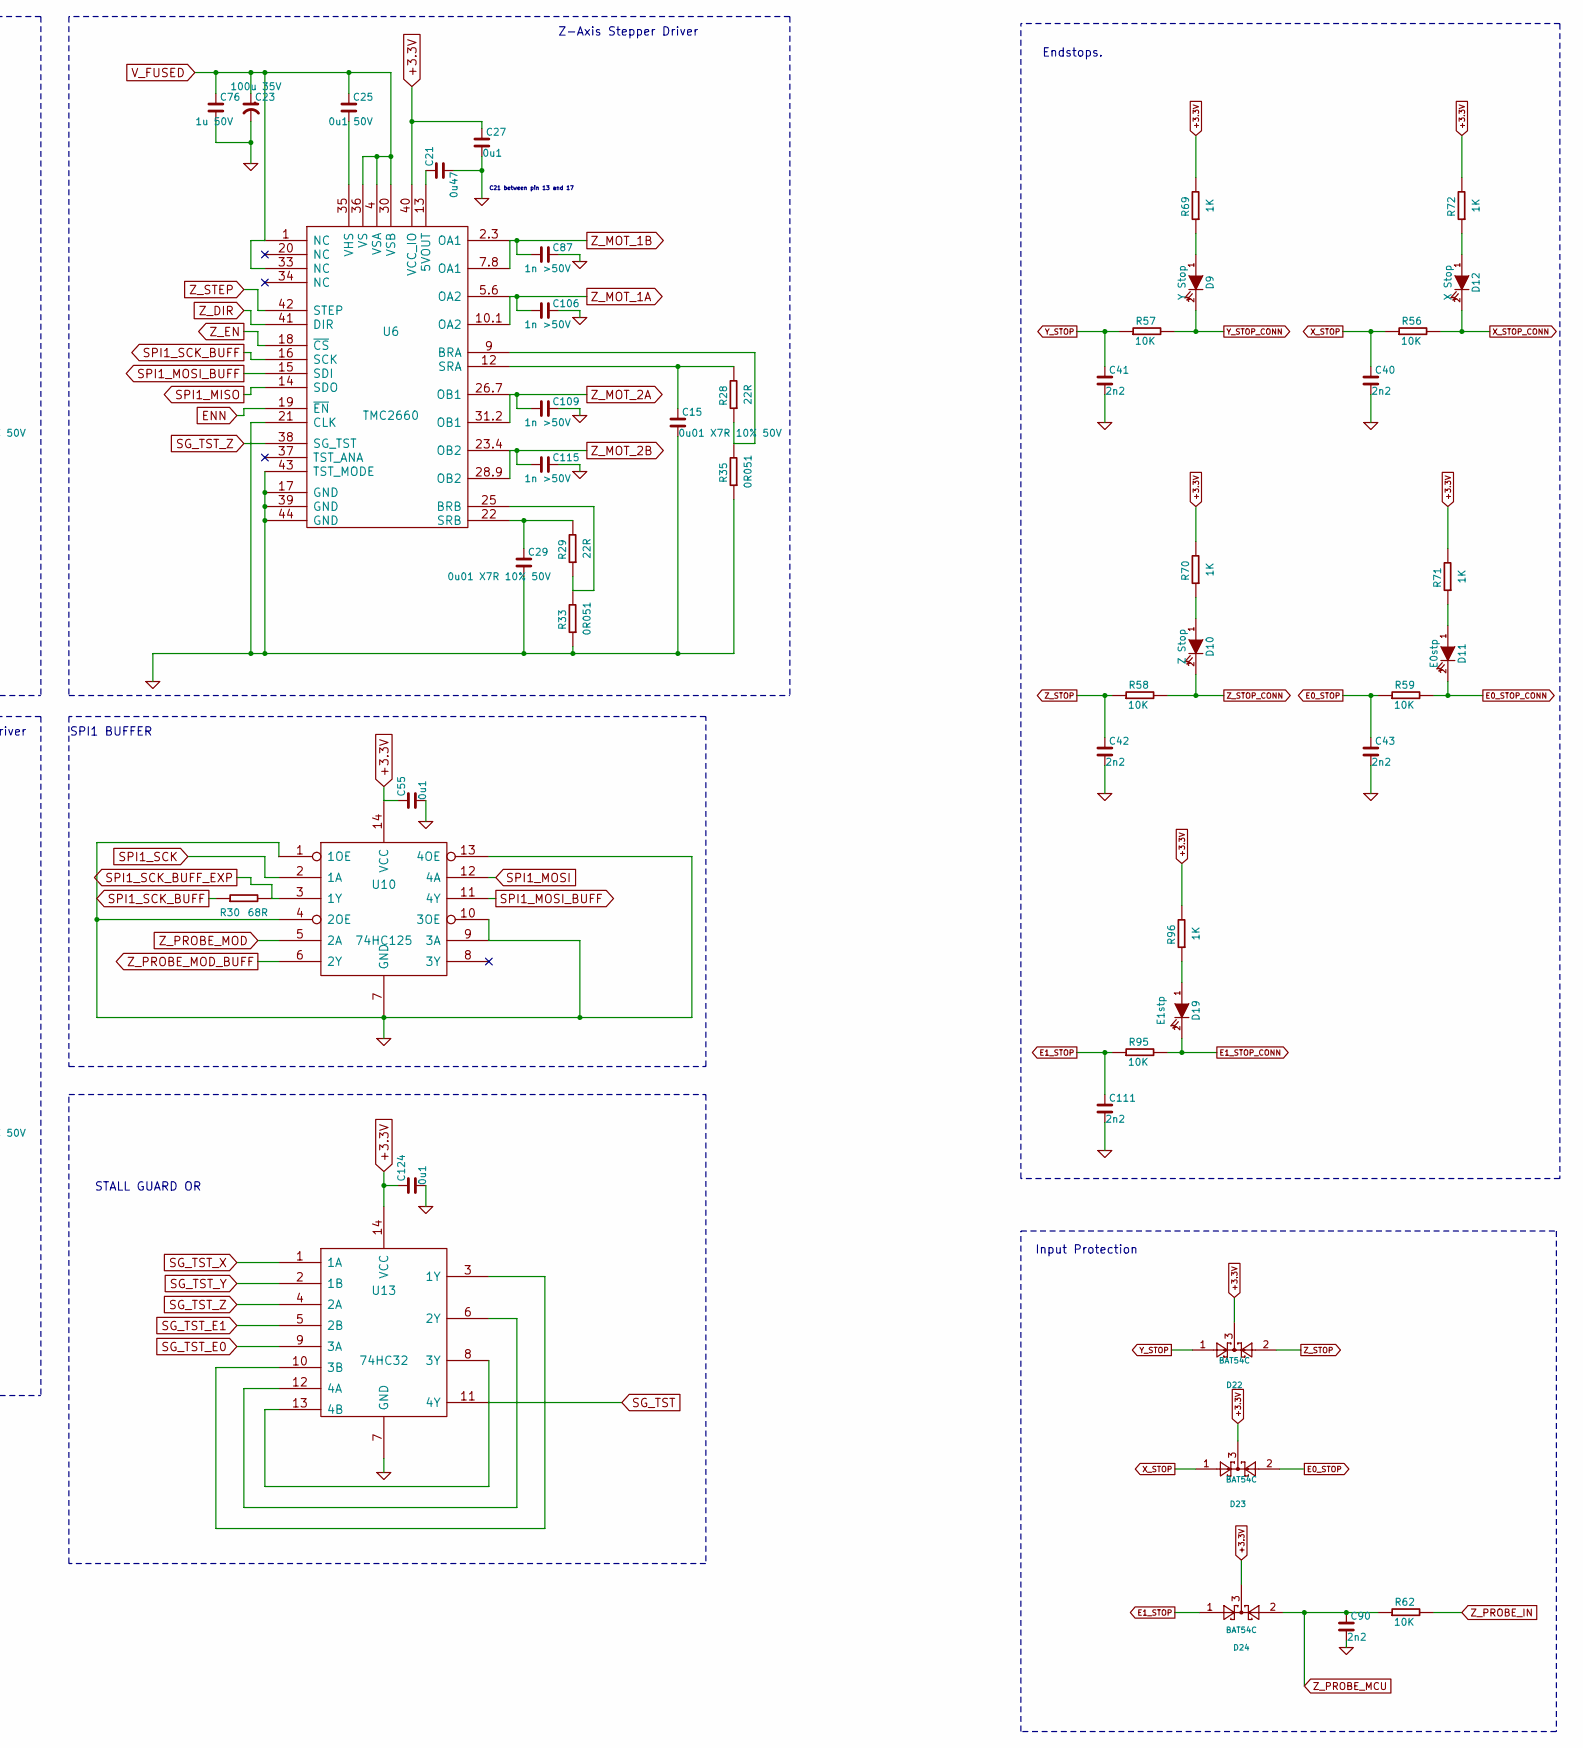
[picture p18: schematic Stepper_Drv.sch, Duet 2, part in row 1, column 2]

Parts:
C14, C15, C28, C29, C38, C39, C56, C57, C105, C110: 0u01 X7R 10% 50V; C_0603
C20, C21, C30, C31, C100: 0u47; C_0603
C22, C23, C32, C33, C102: 100u 35V; C_ELEC_6.3x7.7
C24, C25, C34, C35, C103: 0u1 50V; C_0603
C26, C27, C36, C37, C55, C104, C124: 0u1; C_0603
C40, C41, C42, C43, C90, C111: 2n2; C_0603
C75, C76, C77, C78, C101: 1u 50V; C_0603
C85, C86, C87, C88, C89, C106, C107, C108, C109, C113, C114, C115, C116, C117, C118, C119, C120, C121, C122, C123: 1n >50V; C_0603
D9: Y Stop; D_0603
D10: Z Stop; D_0603
D11: E0stp; D_0603
D12: X Stop; D_0603
D19: E1stp; D_0603
D22, D23, D24: BAT54C; SOT-23-D
R26, R27, R28, R29, R38, R39, R40, R41, R89, R90: 22R; R_0603
R30: 68R; R_0603
R32, R33, R34, R35, R44, R45, R46, R47, R93, R94: 0R051; R_1206
R56, R57, R58, R59, R62, R95: 10K; R_0603
R69, R70, R71, R72, R96: 1K; R_0603
U5, U6, U7, U8, U9: TMC2660
U10: 74HC125; TSSOP-14
U13: 74HC32; TSSOP-14

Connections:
+3.3V: C26.1, C27.1, C36.1, C37.1, C55.1, C104.1, C124.1, D22.3, D23.3, D24.3, R69.2, R70.2, R71.2, R72.2, R96.2, U5.40 (VCC_IO), U6.40 (VCC_IO), U7.40 (VCC_IO), U8.40 (VCC_IO), U9.40 (VCC_IO), U10.14 (VCC), U13.14 (VCC); also elsewhere on the board
E0_DIR: U8.41 (DIR); also elsewhere on the board
E0_EN: U8.18 (~CS); also elsewhere on the board
E0_MOT_1A: C118.2, U8.5.6 (OA2), U8.10.1 (OA2); also elsewhere on the board
E0_MOT_1B: C116.2, U8.2.3 (OA1), U8.7.8 (OA1); also elsewhere on the board
E0_MOT_2A: C120.2, U8.26.7 (OB1), U8.31.2 (OB1); also elsewhere on the board
E0_MOT_2B: C122.2, U8.23.4 (OB2), U8.28.9 (OB2); also elsewhere on the board
E0_STEP: U8.42 (STEP); also elsewhere on the board
E0_STOP: C43.1, D23.2, R59.1; also elsewhere on the board
E0_STOP_CONN: D11.2 (K), R59.2; also elsewhere on the board
E1_DIR: U9.41 (DIR); also elsewhere on the board
E1_EN: U9.18 (~CS); also elsewhere on the board
E1_MOT_1A: C119.2, U9.5.6 (OA2), U9.10.1 (OA2); also elsewhere on the board
E1_MOT_1B: C117.2, U9.2.3 (OA1), U9.7.8 (OA1); also elsewhere on the board
E1_MOT_2A: C121.2, U9.26.7 (OB1), U9.31.2 (OB1); also elsewhere on the board
E1_MOT_2B: C123.2, U9.23.4 (OB2), U9.28.9 (OB2); also elsewhere on the board
E1_STEP: U9.42 (STEP); also elsewhere on the board
E1_STOP: C111.1, D24.1, R95.1; also elsewhere on the board
E1_STOP_CONN: D19.2 (K), R95.2; also elsewhere on the board
ENN: U5.19 (~EN), U6.19 (~EN), U7.19 (~EN), U8.19 (~EN), U9.19 (~EN); also elsewhere on the board
GND: C14.2, C15.2, C20.2, C21.2, C22.2, C23.2, C26.2, C27.2, C28.2, C29.2, C30.2, C31.2, C32.2, C33.2, C36.2, C37.2, C38.2, C39.2, C40.2, C41.2, C42.2, C43.2, C55.2, C56.2, C57.2, C75.2, C76.2, C77.2, C78.2, C85.1, C86.1, C87.1, C88.1, C89.1, C90.2, C100.2, C101.2, C102.2, C104.2, C105.2, C106.1, C107.1, C108.1, C109.1, C110.2, C111.2, C113.1, C114.1, C115.1, C116.1, C117.1, C118.1, C119.1, C120.1, C121.1, C122.1, C123.1, C124.2, R32.1, R33.1, R34.1, R35.1, R44.1, R45.1, R46.1, R47.1, R93.1, R94.1, U5.17 (GND), U5.21 (CLK), U5.39 (GND), U5.43 (TST_MODE), U5.44 (GND), U6.17 (GND), U6.21 (CLK), U6.39 (GND), U6.43 (TST_MODE), U6.44 (GND), U7.17 (GND), U7.21 (CLK), U7.39 (GND), U7.43 (TST_MODE), U7.44 (GND), U8.17 (GND), U8.21 (CLK), U8.39 (GND), U8.43 (TST_MODE), U8.44 (GND), U9.17 (GND), U9.21 (CLK), U9.39 (GND), U9.43 (TST_MODE), U9.44 (GND), U10.1 (1OE), U10.4 (2OE), U10.7 (GND), U10.9 (3A), U10.10 (3OE), U10.13 (4OE), U13.7 (GND); also elsewhere on the board
unnamed: C14.1, R26.2, U5.12 (SRA)
unnamed: C15.1, R28.2, U6.12 (SRA)
unnamed: C20.1, U5.13 (5VOUT)
unnamed: C21.1, U6.13 (5VOUT)
unnamed: C24.2, U5.35 (VHS)
unnamed: C25.2, U6.35 (VHS)
unnamed: C28.1, R27.2, U5.22 (SRB)
unnamed: C29.1, R29.2, U6.22 (SRB)
unnamed: C30.1, U7.13 (5VOUT)
unnamed: C31.1, U8.13 (5VOUT)
unnamed: C34.2, U7.35 (VHS)
unnamed: C35.2, U8.35 (VHS)
unnamed: C38.1, R38.2, U7.12 (SRA)
unnamed: C39.1, R40.2, U8.12 (SRA)
unnamed: C56.1, R39.2, U7.22 (SRB)
unnamed: C57.1, R41.2, U8.22 (SRB)
unnamed: C100.1, U9.13 (5VOUT)
unnamed: C103.2, U9.35 (VHS)
unnamed: C105.1, R89.2, U9.12 (SRA)
unnamed: C110.1, R90.2, U9.22 (SRB)
unnamed: D9.1 (A), R69.1
unnamed: D10.1 (A), R70.1
unnamed: D11.1 (A), R71.1
unnamed: D12.1 (A), R72.1
unnamed: D19.1 (A), R96.1
unnamed: R26.1, R34.2, U5.9 (BRA)
unnamed: R27.1, R32.2, U5.25 (BRB)
unnamed: R28.1, R35.2, U6.9 (BRA)
unnamed: R29.1, R33.2, U6.25 (BRB)
unnamed: R38.1, R46.2, U7.9 (BRA)
unnamed: R39.1, R44.2, U7.25 (BRB)
unnamed: R40.1, R47.2, U8.9 (BRA)
unnamed: R41.1, R45.2, U8.25 (BRB)
unnamed: R89.1, R94.2, U9.9 (BRA)
unnamed: R90.1, R93.2, U9.25 (BRB)
unnamed: U13.3 (1Y), U13.10 (3B)
unnamed: U13.6 (2Y), U13.12 (4A)
unnamed: U13.8 (3Y), U13.13 (4B)
PB5/TDO: U13.11 (4Y); also elsewhere on the board
SG_TST_E0: U8.38 (SG_TST), U13.9 (3A)
SG_TST_E1: U9.38 (SG_TST), U13.5 (2B)
SG_TST_X: U5.38 (SG_TST), U13.1 (1A)
SG_TST_Y: U7.38 (SG_TST), U13.2 (1B)
SG_TST_Z: U6.38 (SG_TST), U13.4 (2A)
SPI1_MISO: U5.14 (SDO), U6.14 (SDO), U7.14 (SDO), U8.14 (SDO), U9.14 (SDO); also elsewhere on the board
SPI1_MOSI: U10.12 (4A); also elsewhere on the board
SPI1_MOSI_BUFF: U5.15 (SDI), U6.15 (SDI), U7.15 (SDI), U8.15 (SDI), U9.15 (SDI), U10.11 (4Y); also elsewhere on the board
SPI1_SCK: U10.2 (1A); also elsewhere on the board
SPI1_SCK_BUFF: R30.1, U5.16 (SCK), U6.16 (SCK), U7.16 (SCK), U8.16 (SCK), U9.16 (SCK); also elsewhere on the board
SPI1_SCK_BUFF_EXP: R30.2, U10.3 (1Y); also elsewhere on the board
V_FUSED: C22.1, C23.1, C24.1, C25.1, C32.1, C33.1, C34.1, C35.1, C75.1, C76.1, C77.1, C78.1, C101.1, C102.1, C103.1, U5.1 (NC), U5.4 (VSA), U5.30 (VSB), U5.33 (NC), U5.36 (VS), U6.1 (NC), U6.4 (VSA), U6.30 (VSB), U6.33 (NC), U6.36 (VS), U7.1 (NC), U7.4 (VSA), U7.30 (VSB), U7.33 (NC), U7.36 (VS), U8.1 (NC), U8.4 (VSA), U8.30 (VSB), U8.33 (NC), U8.36 (VS), U9.1 (NC), U9.4 (VSA), U9.30 (VSB), U9.33 (NC), U9.36 (VS); also elsewhere on the board
X_DIR: U5.41 (DIR); also elsewhere on the board
X_EN: U5.18 (~CS); also elsewhere on the board
X_MOT_1A: C88.2, U5.5.6 (OA2), U5.10.1 (OA2); also elsewhere on the board
X_MOT_1B: C85.2, U5.2.3 (OA1), U5.7.8 (OA1); also elsewhere on the board
X_MOT_2A: C107.2, U5.26.7 (OB1), U5.31.2 (OB1); also elsewhere on the board
X_MOT_2B: C113.2, U5.23.4 (OB2), U5.28.9 (OB2); also elsewhere on the board
X_STEP: U5.42 (STEP); also elsewhere on the board
X_STOP: C40.1, D23.1, R56.1; also elsewhere on the board
X_STOP_CONN: D12.2 (K), R56.2; also elsewhere on the board
Y_DIR: U7.41 (DIR); also elsewhere on the board
Y_EN: U7.18 (~CS); also elsewhere on the board
Y_MOT_1A: C89.2, U7.5.6 (OA2), U7.10.1 (OA2); also elsewhere on the board
Y_MOT_1B: C86.2, U7.2.3 (OA1), U7.7.8 (OA1); also elsewhere on the board
Y_MOT_2A: C108.2, U7.26.7 (OB1), U7.31.2 (OB1); also elsewhere on the board
Y_MOT_2B: C114.2, U7.23.4 (OB2), U7.28.9 (OB2); also elsewhere on the board
Y_STEP: U7.42 (STEP); also elsewhere on the board
Y_STOP: C41.1, D22.1, R57.1; also elsewhere on the board
Y_STOP_CONN: D9.2 (K), R57.2; also elsewhere on the board
Z_DIR: U6.41 (DIR); also elsewhere on the board
Z_EN: U6.18 (~CS); also elsewhere on the board
Z_MOT_1A: C106.2, U6.5.6 (OA2), U6.10.1 (OA2); also elsewhere on the board
Z_MOT_1B: C87.2, U6.2.3 (OA1), U6.7.8 (OA1); also elsewhere on the board
Z_MOT_2A: C109.2, U6.26.7 (OB1), U6.31.2 (OB1); also elsewhere on the board
Z_MOT_2B: C115.2, U6.23.4 (OB2), U6.28.9 (OB2); also elsewhere on the board
Z_PROBE_IN: R62.2; also elsewhere on the board
Z_PROBE_MCU: C90.1, D24.2, R62.1; also elsewhere on the board
Z_PROBE_MOD: U10.5 (2A); also elsewhere on the board
Z_PROBE_MOD_BUFF: U10.6 (2Y); also elsewhere on the board
Z_STEP: U6.42 (STEP); also elsewhere on the board
Z_STOP: C42.1, D22.2, R58.1; also elsewhere on the board
Z_STOP_CONN: D10.2 (K), R58.2; also elsewhere on the board

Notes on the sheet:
Endstops.
Extruder 0 Stepper Driver
Y-Axis Stepper Driver
X-Axis Stepper Driver
Extruder 1 Stepper Driver
SPI1 BUFFER
C20 between pin 13 and 17
C30 between pin 13 and 17
Z-Axis Stepper Driver
C21 between pin 13 and 17
STALL GUARD OR
Input Protection

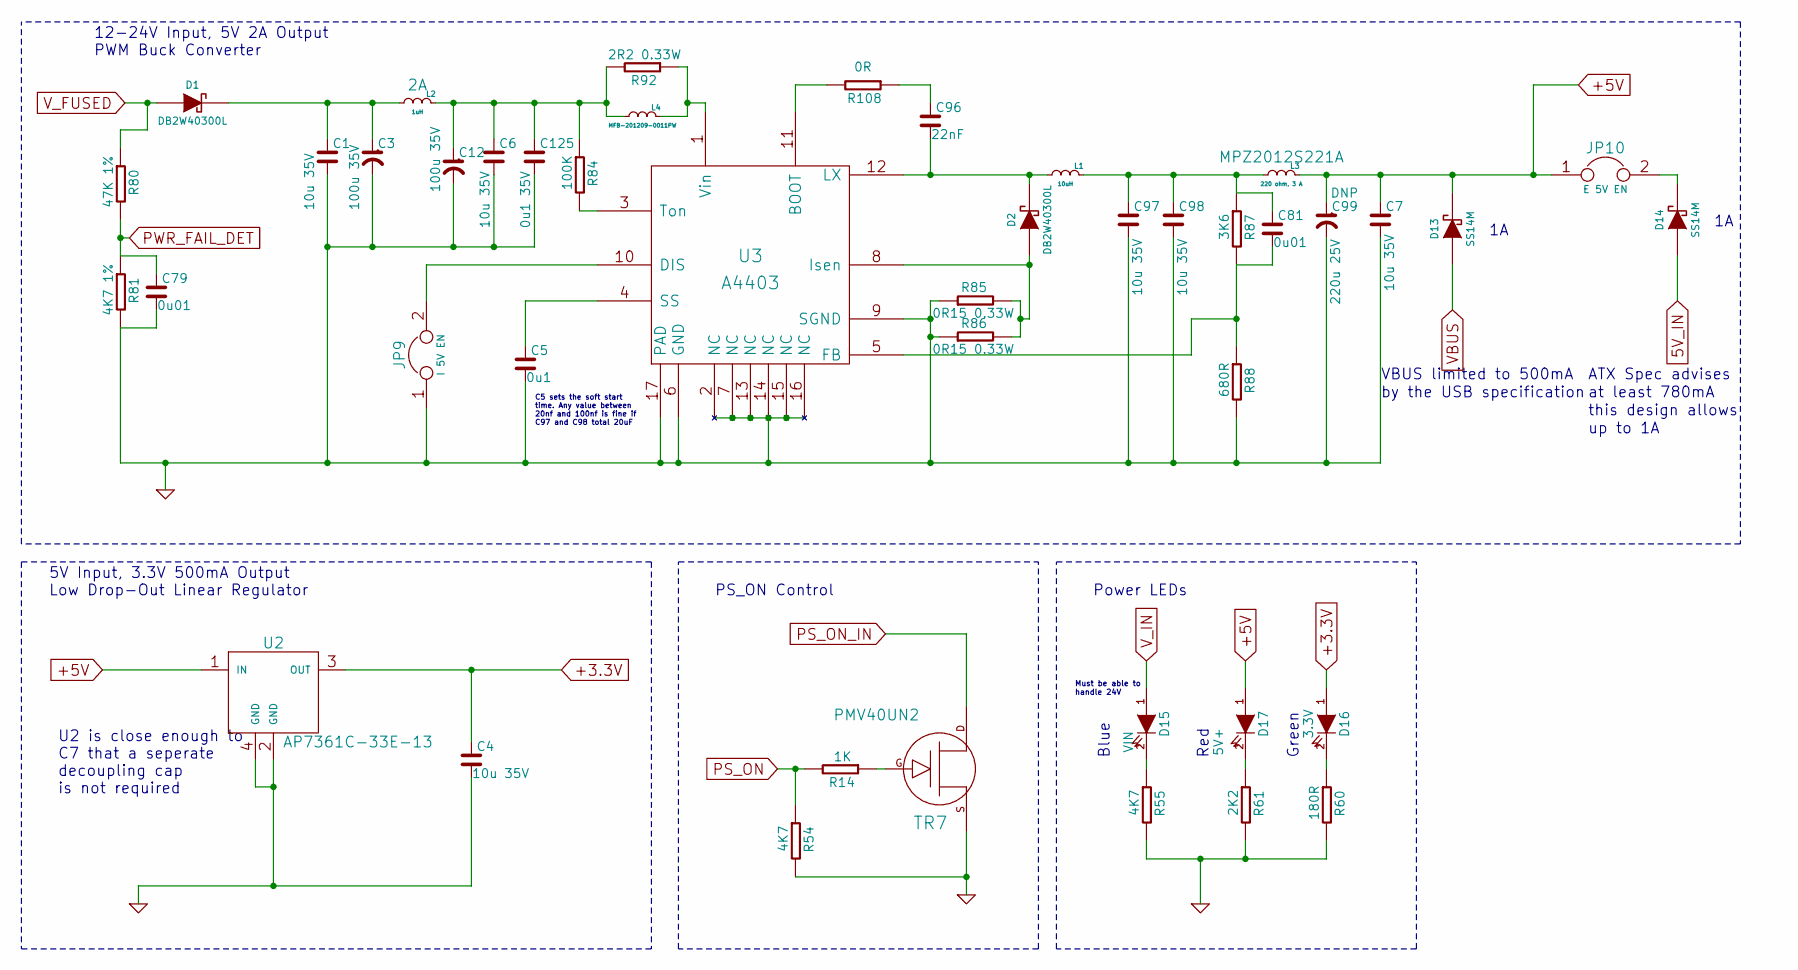
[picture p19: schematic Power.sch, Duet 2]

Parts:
C1, C4, C6, C7, C97, C98: 10u 35V; C_1206
C3, C12: 100u 35V; C_ELEC_6.3x7.7
C5: 0u1; C_0603
C79, C81: 0u01; C_0603
C96: 22nF; C_0603
C99: 220u 25V; C_ELEC_6.3x7.7; Rating DNP
C125: 0u1 35V; C_0603
D1, D2: DB2W40300L; D_SOD-123F
D13, D14: SS14M; uSMA
D15: VIN; D_0603
D16: 3.3V; D_0603
D17: 5V+; D_0603
JP9: I 5V EN; JUMPER
JP10: E 5V EN; JUMPER
L1: 10uH; L_6x6
L2: 1uH; C_1210; Rating 2A
L3: 220 ohm, 3 A; R_0805; Rating MPZ2012S221A
L4: MFB-201209-0011PW; R_0805
R14: 1K; R_0603
R54, R55: 4K7; R_0603
R60: 180R; R_0603
R61: 2K2; R_0603
R80: 47K 1%; R_0603
R81: 4K7 1%; R_0603
R84: 100K; R_0603
R85, R86: 0R15 0.33W; R_0805
R87: 3K6; R_0603
R88: 680R; R_0603
R92: 2R2 0.33W; R_0805
R108: 0R; R_0603
TR7: PMV40UN2; SOT-23
U2: AP7361C-33E-13; SOT-223
U3: A4403; QFN16-4x4

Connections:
5V_IN: D14.1 (A); also elsewhere on the board
+3.3V: C4.1, D16.1 (A), U2.3 (OUT); also elsewhere on the board
+5V: C7.1, C99.1, D13.2 (K), D17.1 (A), JP10.1, L3.1 (A), U2.1 (IN); also elsewhere on the board
GND: C1.2, C3.2, C4.2, C5.2, C6.2, C7.2, C12.2, C79.2, C97.2, C98.2, C99.2, C125.2, JP9.1, R54.2, R55.2, R60.2, R61.2, R81.2, R85.1, R86.1, R88.2, TR7.S, U2.2 (GND), U2.4 (GND), U3.2 (NC), U3.6 (GND), U3.7 (NC), U3.9 (SGND), U3.13 (NC), U3.14 (NC), U3.15 (NC), U3.16 (NC), U3.17 (PAD); also elsewhere on the board
unnamed: C1.1, C3.1, D1.1 (K), L2.2 (B)
unnamed: C5.1, U3.4 (SS)
unnamed: C6.1, C12.1, C125.1, L2.1 (A), L4.2 (B), R84.1, R92.2
unnamed: C81.1, C97.1, C98.1, L1.1 (A), L3.2 (B), R87.1
unnamed: C81.2, R87.2, R88.1, U3.5 (FB)
unnamed: C96.1, R108.1
unnamed: C96.2, D2.1 (K), L1.2 (B), U3.12 (LX)
unnamed: D2.2 (A), R85.2, R86.2, U3.8 (Isen)
unnamed: D14.2 (K), JP10.2
unnamed: D15.2 (K), R55.1
unnamed: D16.2 (K), R60.1
unnamed: D17.2 (K), R61.1
unnamed: JP9.2, U3.10 (DIS)
unnamed: L4.1 (A), R92.1, U3.1 (Vin)
unnamed: R14.1, TR7.G
unnamed: R84.2, U3.3 (Ton)
unnamed: R108.2, U3.11 (BOOT)
PS_ON: R14.2, R54.1; also elsewhere on the board
PS_ON_IN: TR7.D; also elsewhere on the board
PWR_FAIL_DET: C79.1, R80.2, R81.1; also elsewhere on the board
VBUS: D13.1 (A); also elsewhere on the board
V_FUSED: D1.2 (A), R80.1; also elsewhere on the board
V_IN: D15.1 (A); also elsewhere on the board

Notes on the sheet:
PS_ON Control
up to 1A
this design allows
at least 780mA
ATX Spec advises
by the USB specification
VBUS limited to 500mA
5V Input, 3.3V 500mA Output Low Drop-Out Linear Regulator
12-24V Input, 5V 2A Output PWM Buck Converter
C5 sets the soft start time. Any value between 20nf and 100nf is fine if C97 and C98 total 20uF
Power LEDs
Must be able to handle 24V
Blue
Red
Green
U2 is close enough to C7 that a seperate decoupling cap is not required

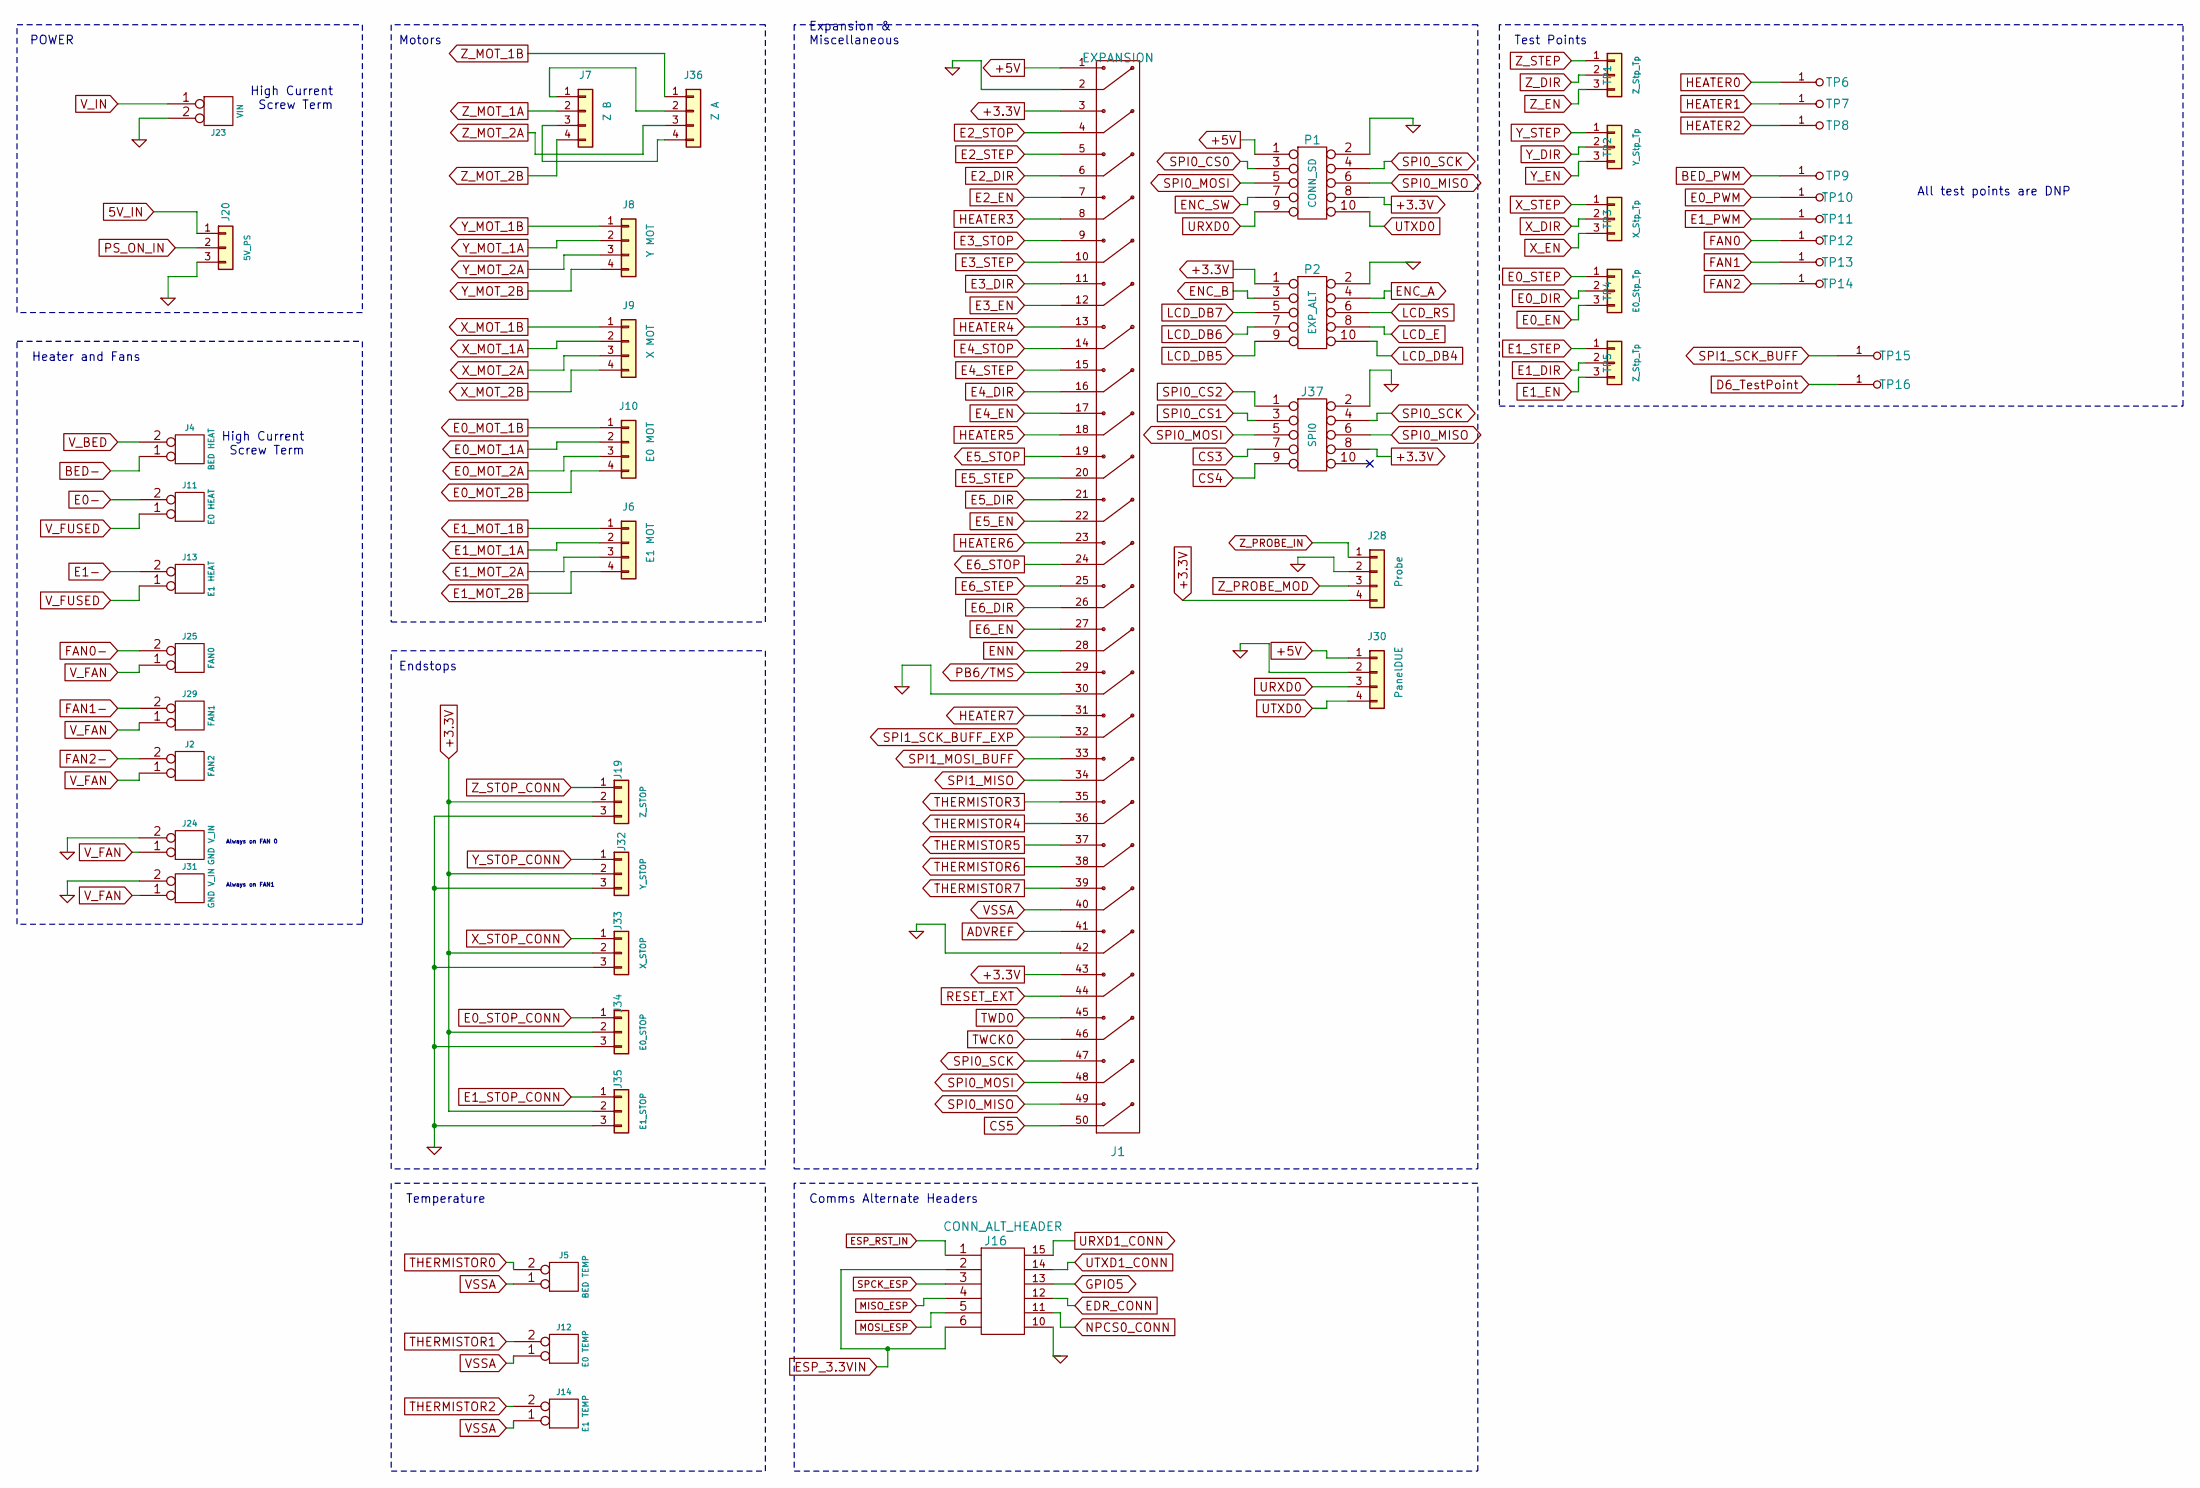
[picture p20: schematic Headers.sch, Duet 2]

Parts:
J1: EXPANSION; PIN_ARRAY_25X2
J2: FAN2; PIN_ARRAY_2X1
J4: BED HEAT; TERM_2-WAY_6.35mm
J5: BED TEMP; PIN_ARRAY_2X1
J6: E1 MOT; PIN_ARRAY_4x1
J7: Z B; PIN_ARRAY_4x1
J8: Y MOT; PIN_ARRAY_4x1
J9: X MOT; PIN_ARRAY_4x1
J10: E0 MOT; PIN_ARRAY_4x1
J11: E0 HEAT; 3.5MM_2X1
J12: E0 TEMP; PIN_ARRAY_2X1
J13: E1 HEAT; 3.5MM_2X1
J14: E1 TEMP; PIN_ARRAY_2X1
J16: CONN_ALT_HEADER; CONN_ALT_HEADER_v2
J19: Z_STOP; PIN_ARRAY_3X1
J20: 5V_PS; PIN_ARRAY_3X1
J23: VIN; TERM_2-WAY_6.35mm
J24, J31: GND V_IN; PIN_ARRAY_2X1
J25: FAN0; PIN_ARRAY_2X1
J28: Probe; PIN_ARRAY_4x1
J29: FAN1; PIN_ARRAY_2X1
J30: PanelDUE; PIN_ARRAY_4x1
J32: Y_STOP; PIN_ARRAY_3X1
J33: X_STOP; PIN_ARRAY_3X1
J34: E0_STOP; PIN_ARRAY_3X1
J35: E1_STOP; PIN_ARRAY_3X1
J36: Z A; PIN_ARRAY_4x1
J37: SPI0; MAX_TEMP_DB
P1: CONN_SD; IDC_PIN_ARRAY_5x2
P2: EXP_ALT; IDC_PIN_ARRAY_5x2
TP1, TP5: Z_Stp_Tp; CONN_3x1
TP2: Y_Stp_Tp; CONN_3x1
TP3: X_Stp_Tp; CONN_3x1
TP4: E0_Stp_Tp; CONN_3x1
TP6, TP7, TP8, TP9, TP10, TP11, TP12, TP13, TP14, TP15, TP16: TP; TP_via

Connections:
5V_IN: J20.1; also elsewhere on the board
+3.3V: J1.3, J1.43, J19.2, J28.4, J32.2, J33.2, J34.2, J35.2, J37.8, P1.8, P2.1; also elsewhere on the board
+5V: J1.1, J30.1, P1.1; also elsewhere on the board
ADVREF: J1.41; also elsewhere on the board
BED-: J4.1; also elsewhere on the board
BED_PWM: TP9.1; also elsewhere on the board
CS3: J37.7; also elsewhere on the board
CS4: J37.9; also elsewhere on the board
CS5: J1.50; also elsewhere on the board
D6_TestPoint: TP16.1; also elsewhere on the board
E0-: J11.2 (PM); also elsewhere on the board
E0_DIR: TP4.2; also elsewhere on the board
E0_EN: TP4.3; also elsewhere on the board
E0_MOT_1A: J10.2; also elsewhere on the board
E0_MOT_1B: J10.1; also elsewhere on the board
E0_MOT_2A: J10.3; also elsewhere on the board
E0_MOT_2B: J10.4; also elsewhere on the board
E0_PWM: TP10.1; also elsewhere on the board
E0_STEP: TP4.1; also elsewhere on the board
E0_STOP_CONN: J34.1; also elsewhere on the board
E1-: J13.2 (PM); also elsewhere on the board
E1_DIR: TP5.2; also elsewhere on the board
E1_EN: TP5.3; also elsewhere on the board
E1_MOT_1A: J6.2; also elsewhere on the board
E1_MOT_1B: J6.1; also elsewhere on the board
E1_MOT_2A: J6.3; also elsewhere on the board
E1_MOT_2B: J6.4; also elsewhere on the board
E1_PWM: TP11.1; also elsewhere on the board
E1_STEP: TP5.1; also elsewhere on the board
E1_STOP_CONN: J35.1; also elsewhere on the board
E2_DIR: J1.6; also elsewhere on the board
E2_EN: J1.7; also elsewhere on the board
E2_STEP: J1.5; also elsewhere on the board
E2_STOP: J1.4; also elsewhere on the board
E3_DIR: J1.11; also elsewhere on the board
E3_EN: J1.12; also elsewhere on the board
E3_STEP: J1.10; also elsewhere on the board
E3_STOP: J1.9; also elsewhere on the board
E4_DIR: J1.16; also elsewhere on the board
E4_EN: J1.17; also elsewhere on the board
E4_STEP: J1.15; also elsewhere on the board
E4_STOP: J1.14; also elsewhere on the board
E5_DIR: J1.21; also elsewhere on the board
E5_EN: J1.22; also elsewhere on the board
E5_STEP: J1.20; also elsewhere on the board
E5_STOP: J1.19; also elsewhere on the board
E6_DIR: J1.26; also elsewhere on the board
E6_EN: J1.27; also elsewhere on the board
E6_STEP: J1.25; also elsewhere on the board
E6_STOP: J1.24; also elsewhere on the board
EDR_CONN: J16.12; also elsewhere on the board
ENC_A: P2.4; also elsewhere on the board
ENC_B: P2.3; also elsewhere on the board
ENC_SW: P1.7; also elsewhere on the board
ENN: J1.28; also elsewhere on the board
ESP_3.3VIN: J16.2, J16.6; also elsewhere on the board
ESP_RST_IN: J16.1; also elsewhere on the board
FAN0: TP12.1; also elsewhere on the board
FAN0-: J25.2 (PM); also elsewhere on the board
FAN1: TP13.1; also elsewhere on the board
FAN1-: J29.2 (PM); also elsewhere on the board
FAN2: TP14.1; also elsewhere on the board
FAN2-: J2.2 (PM); also elsewhere on the board
GND: J1.2, J1.30, J1.42, J16.10, J19.3, J20.3, J23.2 (PM), J24.2 (PM), J28.2, J30.2, J31.2 (PM), J32.3, J33.3, J34.3, J35.3, J37.2, P1.2, P2.2; also elsewhere on the board
GPIO5: J16.13; also elsewhere on the board
HEATER0: TP6.1; also elsewhere on the board
HEATER1: TP7.1; also elsewhere on the board
HEATER2: TP8.1; also elsewhere on the board
HEATER3: J1.8; also elsewhere on the board
HEATER4: J1.13; also elsewhere on the board
HEATER5: J1.18; also elsewhere on the board
HEATER6: J1.23; also elsewhere on the board
HEATER7: J1.31; also elsewhere on the board
LCD_DB4: P2.10; also elsewhere on the board
LCD_DB5: P2.9; also elsewhere on the board
LCD_DB6: P2.7; also elsewhere on the board
LCD_DB7: P2.5; also elsewhere on the board
LCD_E: P2.8; also elsewhere on the board
LCD_RS: P2.6; also elsewhere on the board
MISO: J16.4; also elsewhere on the board
MOSI_ESP: J16.5; also elsewhere on the board
NPCS0_CONN: J16.11; also elsewhere on the board
unnamed: J7.1, J36.2
unnamed: J7.3, J36.4
PB6/TMS: J1.29; also elsewhere on the board
PS_ON_IN: J20.2; also elsewhere on the board
RESET_EXT: J1.44; also elsewhere on the board
SPCK_ESP: J16.3; also elsewhere on the board
SPI0_CS0: P1.3; also elsewhere on the board
SPI0_CS1: J37.3; also elsewhere on the board
SPI0_CS2: J37.1; also elsewhere on the board
SPI0_MISO: J1.49, J37.6, P1.6; also elsewhere on the board
SPI0_MOSI: J1.48, J37.5, P1.5; also elsewhere on the board
SPI0_SCK: J1.47, J37.4, P1.4; also elsewhere on the board
SPI1_MISO: J1.34; also elsewhere on the board
SPI1_MOSI_BUFF: J1.33; also elsewhere on the board
SPI1_SCK_BUFF: TP15.1; also elsewhere on the board
SPI1_SCK_BUFF_EXP: J1.32; also elsewhere on the board
THERMISTOR0: J5.2 (PM); also elsewhere on the board
THERMISTOR1: J12.2 (PM); also elsewhere on the board
THERMISTOR2: J14.2 (PM); also elsewhere on the board
THERMISTOR3: J1.35; also elsewhere on the board
THERMISTOR4: J1.36; also elsewhere on the board
THERMISTOR5: J1.37; also elsewhere on the board
THERMISTOR6: J1.38; also elsewhere on the board
THERMISTOR7: J1.39; also elsewhere on the board
TWCK0: J1.46; also elsewhere on the board
TWD0: J1.45; also elsewhere on the board
URXD0: J30.3, P1.9; also elsewhere on the board
URXD1_CONN: J16.15; also elsewhere on the board
UTXD0: J30.4, P1.10; also elsewhere on the board
UTXD1_CONN: J16.14; also elsewhere on the board
VSSA: J1.40, J5.1, J12.1, J14.1; also elsewhere on the board
V_BED: J4.2 (PM); also elsewhere on the board
V_FAN: J2.1, J24.1, J25.1, J29.1, J31.1; also elsewhere on the board
V_FUSED: J11.1, J13.1; also elsewhere on the board
V_IN: J23.1; also elsewhere on the board
X_DIR: TP3.2; also elsewhere on the board
X_EN: TP3.3; also elsewhere on the board
X_MOT_1A: J9.2; also elsewhere on the board
X_MOT_1B: J9.1; also elsewhere on the board
X_MOT_2A: J9.3; also elsewhere on the board
X_MOT_2B: J9.4; also elsewhere on the board
X_STEP: TP3.1; also elsewhere on the board
X_STOP_CONN: J33.1; also elsewhere on the board
Y_DIR: TP2.2; also elsewhere on the board
Y_EN: TP2.3; also elsewhere on the board
Y_MOT_1A: J8.2; also elsewhere on the board
Y_MOT_1B: J8.1; also elsewhere on the board
Y_MOT_2A: J8.3; also elsewhere on the board
Y_MOT_2B: J8.4; also elsewhere on the board
Y_STEP: TP2.1; also elsewhere on the board
Y_STOP_CONN: J32.1; also elsewhere on the board
Z_DIR: TP1.2; also elsewhere on the board
Z_EN: TP1.3; also elsewhere on the board
Z_MOT_1A: J7.2; also elsewhere on the board
Z_MOT_1B: J36.1; also elsewhere on the board
Z_MOT_2A: J36.3; also elsewhere on the board
Z_MOT_2B: J7.4; also elsewhere on the board
Z_PROBE_IN: J28.1; also elsewhere on the board
Z_PROBE_MOD: J28.3; also elsewhere on the board
Z_STEP: TP1.1; also elsewhere on the board
Z_STOP_CONN: J19.1; also elsewhere on the board

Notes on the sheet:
High Current Screw Term
Always on FAN 0
Always on FAN1
POWER
Heater and Fans
Temperature
Motors
Endstops
Expansion & Miscellaneous
Comms Alternate Headers
Test Points
All test points are DNP

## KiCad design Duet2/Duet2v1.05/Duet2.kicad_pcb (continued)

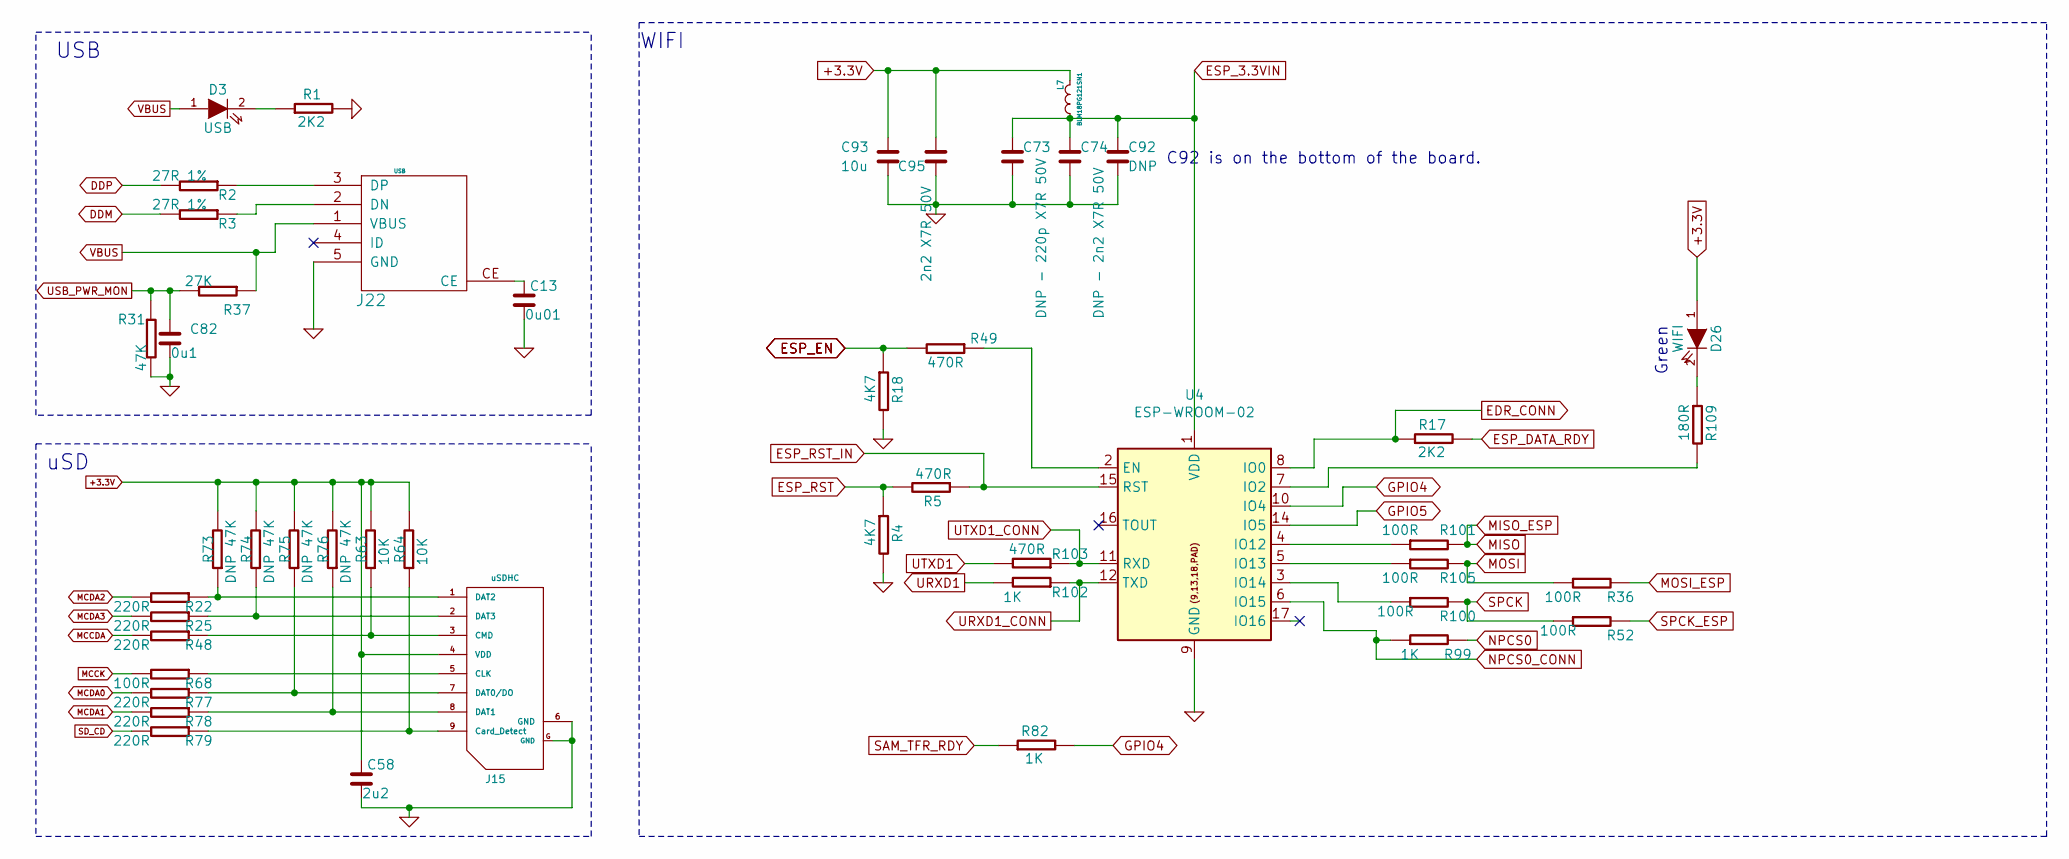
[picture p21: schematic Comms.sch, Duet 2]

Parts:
C13: 0u01; C_0603
C58: 2u2; C_0603
C73: DNP - 220p X7R 50V; C_0603
C74: DNP - 2n2 X7R 50V; C_0603
C82: 0u1; C_0603
C92: DNP; C_0603
C93: 10u; C_0805
C95: 2n2 X7R 50V; C_0603
D3: USB; D_0603
D26: WIFI; D_0603
J15: uSDHC; uSD_SKT
J22: USB; uUSB_new
L7: BLM18PG121SN1; L_0603_1608Metric
R1, R17: 2K2; R_0603
R2, R3: 27R 1%; R_0603
R4, R18: 4K7; R_0603
R5, R49, R103: 470R; R_0603
R22, R25, R48, R77, R78, R79: 220R; R_0603
R31: 47K; R_0603
R36, R52, R68, R100, R101, R105: 100R; R_0603
R37: 27K; R_0603
R63, R64: 10K; R_0603
R73, R74, R75, R76: DNP 47K; R_0603
R82, R99, R102: 1K; R_0603
R109: 180R; R_0603
U4: ESP-WROOM-02; Part Number ESP-WROOM-02/U (Internal and External A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

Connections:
+3.3V: C58.1, C93.1, C95.2, D26.1 (A), J15.4 (VDD), L7.1 (A), R63.2, R64.2, R73.2, R74.2, R75.2, R76.2; also elsewhere on the board
DDM: R3.2; also elsewhere on the board
DDP: R2.2; also elsewhere on the board
EDR_CONN: R17.1, U4.8 (IO0); also elsewhere on the board
ESP_3.3VIN: C73.1, C74.1, C92.1, L7.2 (B), U4.1 (VDD); also elsewhere on the board
ESP_DATA_RDY: R17.2; also elsewhere on the board
ESP_EN: R18.1, R49.2; also elsewhere on the board
ESP_RST: R4.1, R5.2; also elsewhere on the board
ESP_RST_IN: R5.1, U4.15 (RST); also elsewhere on the board
GND: C13.2, C58.2, C73.2, C74.2, C82.2, C92.2, C93.2, C95.1, J15.6 (GND), J15.G (GND), J22.5 (GND), R1.2, R4.2, R18.2, R31.2, U4.9 (GND), U4.13 (GND), U4.18 (GND), U4.19 (GND); also elsewhere on the board
GPIO4: R82.2, U4.10 (IO4)
GPIO5: U4.14 (IO5); also elsewhere on the board
MCCDA: R48.2; also elsewhere on the board
MCCK: R68.2; also elsewhere on the board
MCDA0: R77.2; also elsewhere on the board
MCDA1: R78.2; also elsewhere on the board
MCDA2: R22.2; also elsewhere on the board
MCDA3: R25.2; also elsewhere on the board
MISO: R101.2; also elsewhere on the board
MOSI: R36.1, R105.2; also elsewhere on the board
MOSI_ESP: R36.2; also elsewhere on the board
NPCS0: R99.2; also elsewhere on the board
NPCS0_CONN: R99.1, U4.6 (IO15); also elsewhere on the board
unnamed: C13.1, J22.CE
unnamed: D3.2 (K), R1.1
unnamed: D26.2 (K), R109.1
unnamed: J15.1 (DAT2), R22.1, R73.1
unnamed: J15.2 (DAT3), R25.1, R74.1
unnamed: J15.3 (CMD), R48.1, R63.1
unnamed: J15.5 (CLK), R68.1
unnamed: J15.7 (DAT0/DO), R75.1, R77.1
unnamed: J15.8 (DAT1), R76.1, R78.1
unnamed: J15.9 (Card_Detect), R64.1, R79.1
unnamed: J22.2 (DN), R3.1
unnamed: J22.3 (DP), R2.1
unnamed: R49.1, U4.2 (EN)
unnamed: R100.1, U4.3 (IO14)
unnamed: R101.1, U4.4 (IO12)
unnamed: R105.1, U4.5 (IO13)
unnamed: R109.2, U4.7 (IO2)
SAM_TFR_RDY: R82.1; also elsewhere on the board
SD_CD: R79.2; also elsewhere on the board
SPCK: R52.1, R100.2; also elsewhere on the board
SPCK_ESP: R52.2; also elsewhere on the board
URXD1: R102.2; also elsewhere on the board
URXD1_CONN: R102.1, U4.12 (TXD); also elsewhere on the board
USB_PWR_MON: C82.1, R31.1, R37.2; also elsewhere on the board
UTXD1: R103.2; also elsewhere on the board
UTXD1_CONN: R103.1, U4.11 (RXD); also elsewhere on the board
VBUS: D3.1 (A), J22.1 (VBUS), R37.1; also elsewhere on the board

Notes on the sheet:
uSD
WIFI
USB
C92 is on the bottom of the board.
Green

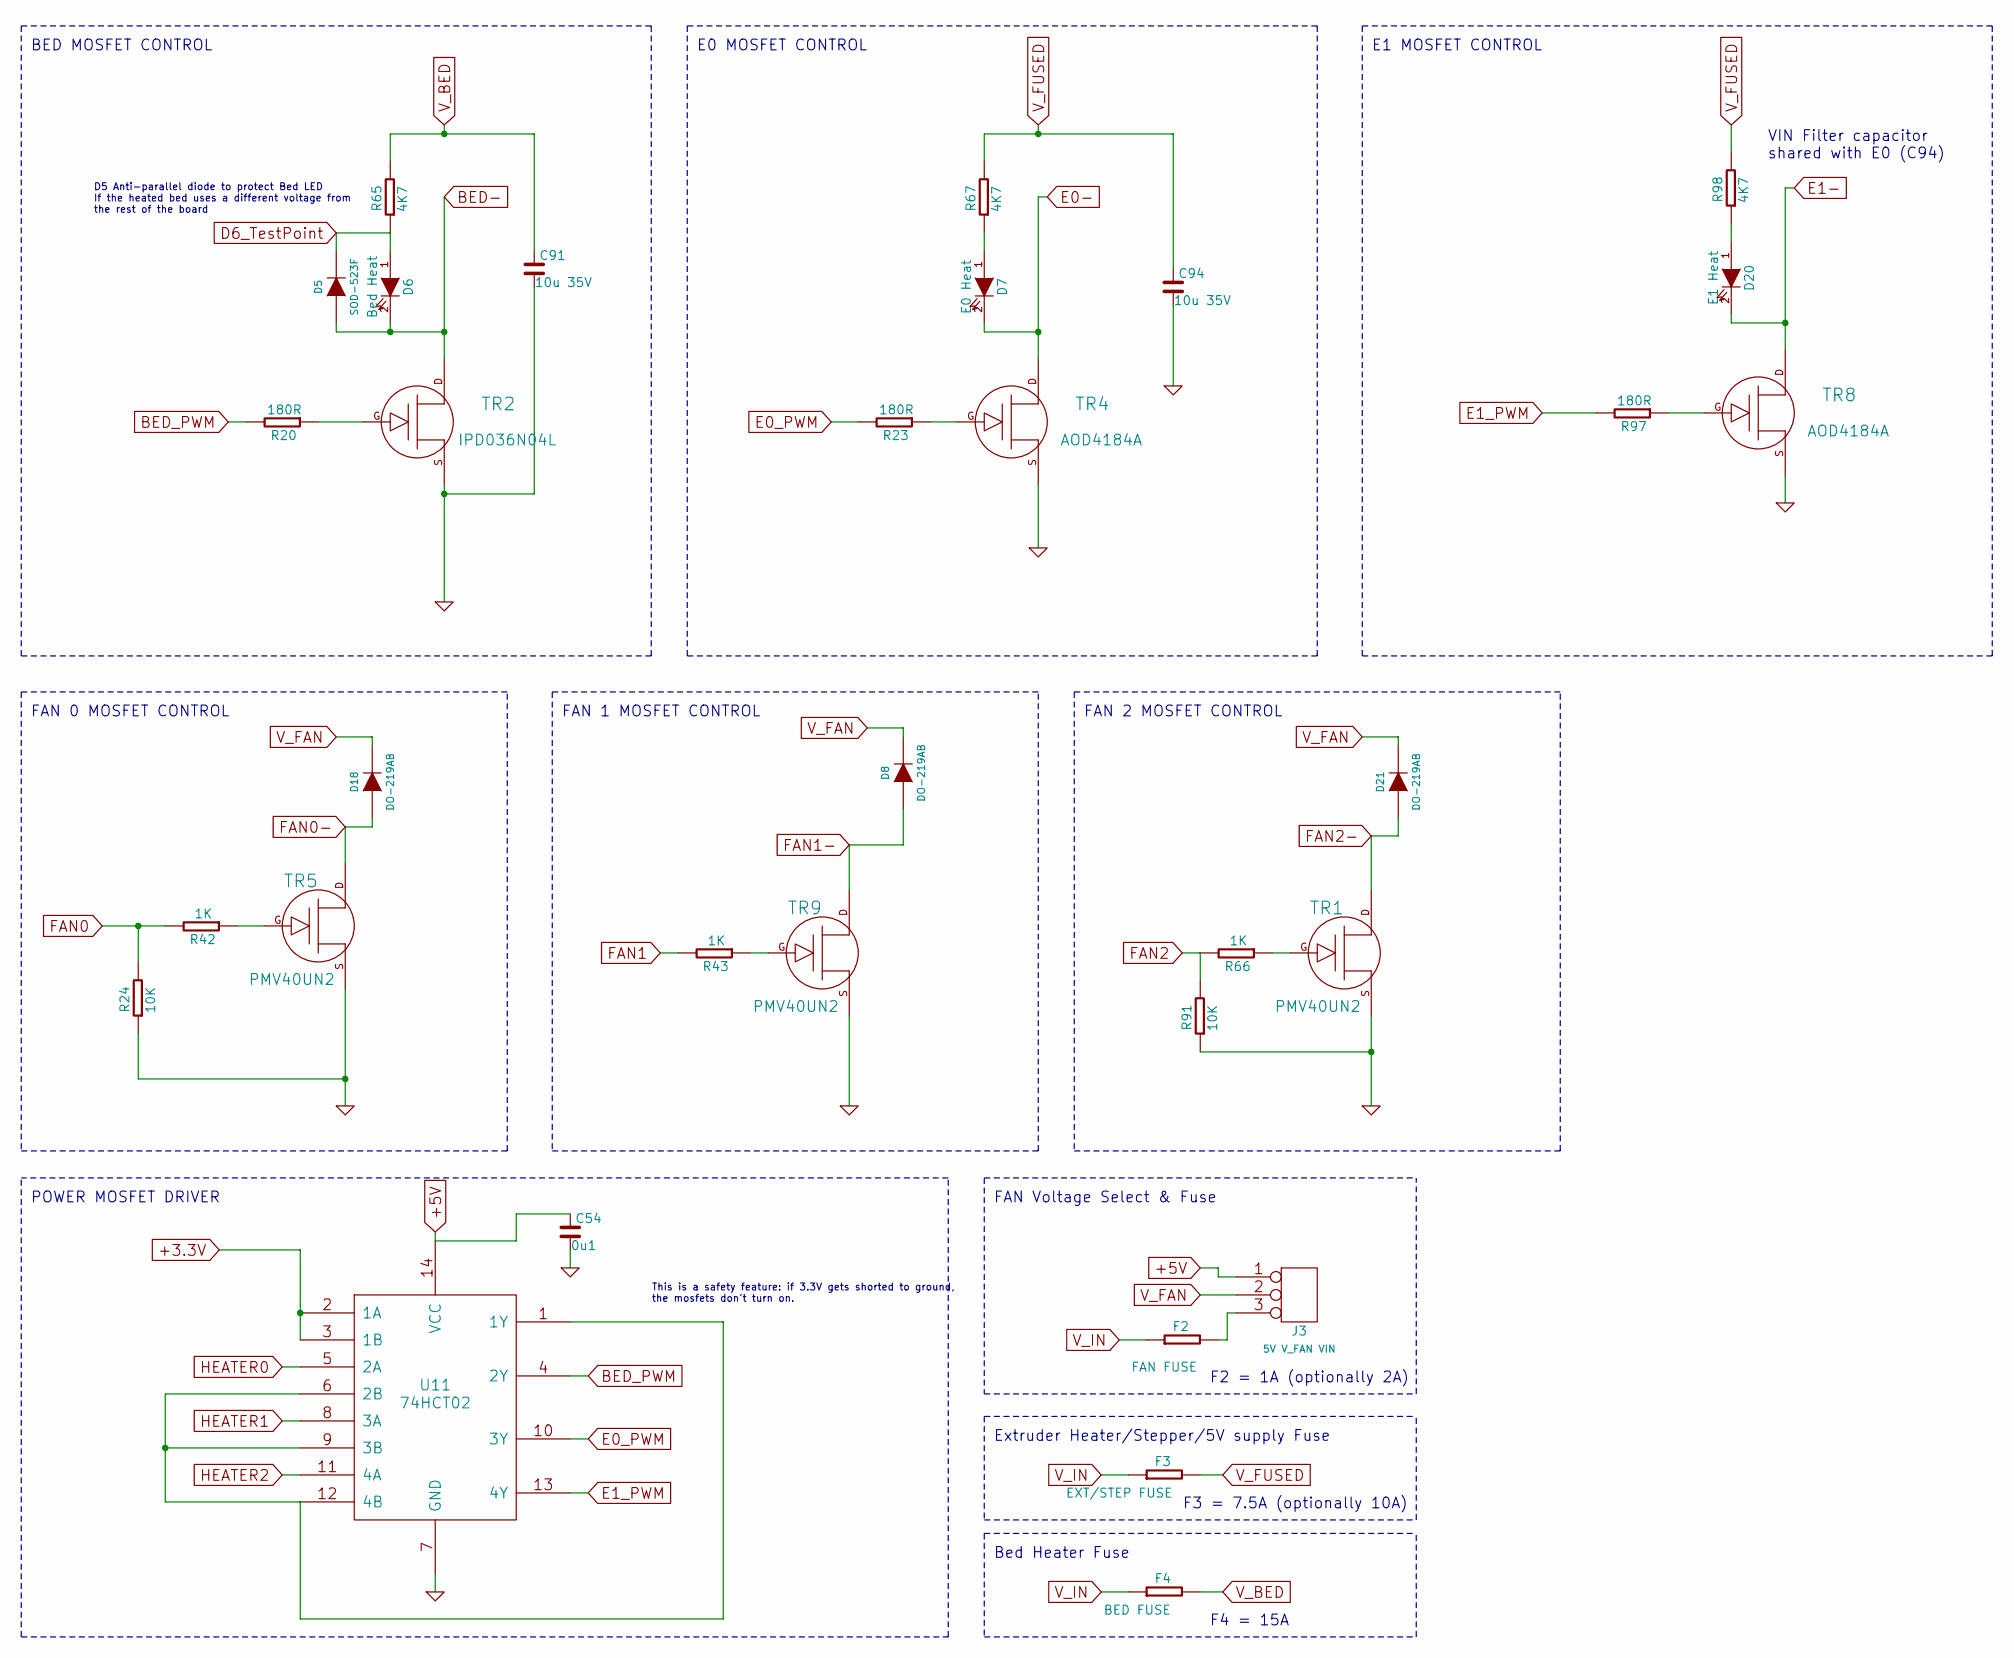
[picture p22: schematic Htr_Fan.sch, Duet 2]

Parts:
C54: 0u1; C_0603
C91, C94: 10u 35V; C_1206
D5: SOD-523F
D6: Bed Heat; D_0603
D7: E0 Heat; D_0603
D8, D18, D21: DO-219AB
D20: E1 Heat; D_0603
F2: FAN FUSE; MCCQ-122-minibladefuseholder
F3: EXT/STEP FUSE; MCCQ-122-minibladefuseholder
F4: BED FUSE; MCCQ-122-minibladefuseholder
J3: 5V V_FAN VIN; CONN_3x1
R20, R23, R97: 180R; R_0603
R24, R91: 10K; R_0603
R42, R43, R66: 1K; R_0603
R65, R67, R98: 4K7; R_0603
TR1, TR5, TR9: PMV40UN2; SOT-23
TR2: IPD036N04L; D-PAK
TR4, TR8: AOD4184A; D-PAK
U11: 74HCT02; TSSOP-14

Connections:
+3.3V: U11.2 (1A), U11.3 (1B); also elsewhere on the board
+5V: C54.1, J3.1, U11.14 (VCC); also elsewhere on the board
BED-: D5.2 (A), D6.2 (K), TR2.D; also elsewhere on the board
BED_PWM: R20.2, U11.4 (2Y); also elsewhere on the board
D6_TestPoint: D5.1 (K), D6.1 (A), R65.1; also elsewhere on the board
E0-: D7.2 (K), TR4.D; also elsewhere on the board
E0_PWM: R23.2, U11.10 (3Y); also elsewhere on the board
E1-: D20.2 (K), TR8.D; also elsewhere on the board
E1_PWM: R97.2, U11.13 (4Y); also elsewhere on the board
FAN0: R24.2, R42.2; also elsewhere on the board
FAN0-: D18.2 (A), TR5.D; also elsewhere on the board
FAN1: R43.2; also elsewhere on the board
FAN1-: D8.2 (A), TR9.D; also elsewhere on the board
FAN2: R66.2, R91.2; also elsewhere on the board
FAN2-: D21.2 (A), TR1.D; also elsewhere on the board
GND: C54.2, C91.2, C94.2, R24.1, R91.1, TR1.S, TR2.S, TR4.S, TR5.S, TR8.S, TR9.S, U11.7 (GND); also elsewhere on the board
HEATER0: U11.5 (2A); also elsewhere on the board
HEATER1: U11.8 (3A); also elsewhere on the board
HEATER2: U11.11 (4A); also elsewhere on the board
unnamed: D7.1 (A), R67.1
unnamed: D20.1 (A), R98.1
unnamed: F2.2, J3.3
unnamed: R20.1, TR2.G
unnamed: R23.1, TR4.G
unnamed: R42.1, TR5.G
unnamed: R43.1, TR9.G
unnamed: R66.1, TR1.G
unnamed: R97.1, TR8.G
unnamed: U11.1 (1Y), U11.6 (2B), U11.9 (3B), U11.12 (4B)
V_BED: C91.1, F4.2, R65.2; also elsewhere on the board
V_FAN: D8.1 (K), D18.1 (K), D21.1 (K), J3.2 (PM); also elsewhere on the board
V_FUSED: C94.1, F3.2, R67.2, R98.2; also elsewhere on the board
V_IN: F2.1, F3.1, F4.1; also elsewhere on the board

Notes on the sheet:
FAN 0 MOSFET CONTROL
E0 MOSFET CONTROL
BED MOSFET CONTROL
E1 MOSFET CONTROL
FAN 1 MOSFET CONTROL
POWER MOSFET DRIVER
This is a safety feature: if 3.3V gets shorted to ground, the mosfets don't turn on.
FAN 2 MOSFET CONTROL
D5 Anti-parallel diode to protect Bed LED If the heated bed uses a different voltage from the rest of the board
FAN Voltage Select & Fuse
VIN Filter capacitor shared with E0 (C94)
Extruder Heater/Stepper/5V supply Fuse
Bed Heater Fuse
F2 = 1A (optionally 2A)
F3 = 7.5A (optionally 10A)
F4 = 15A

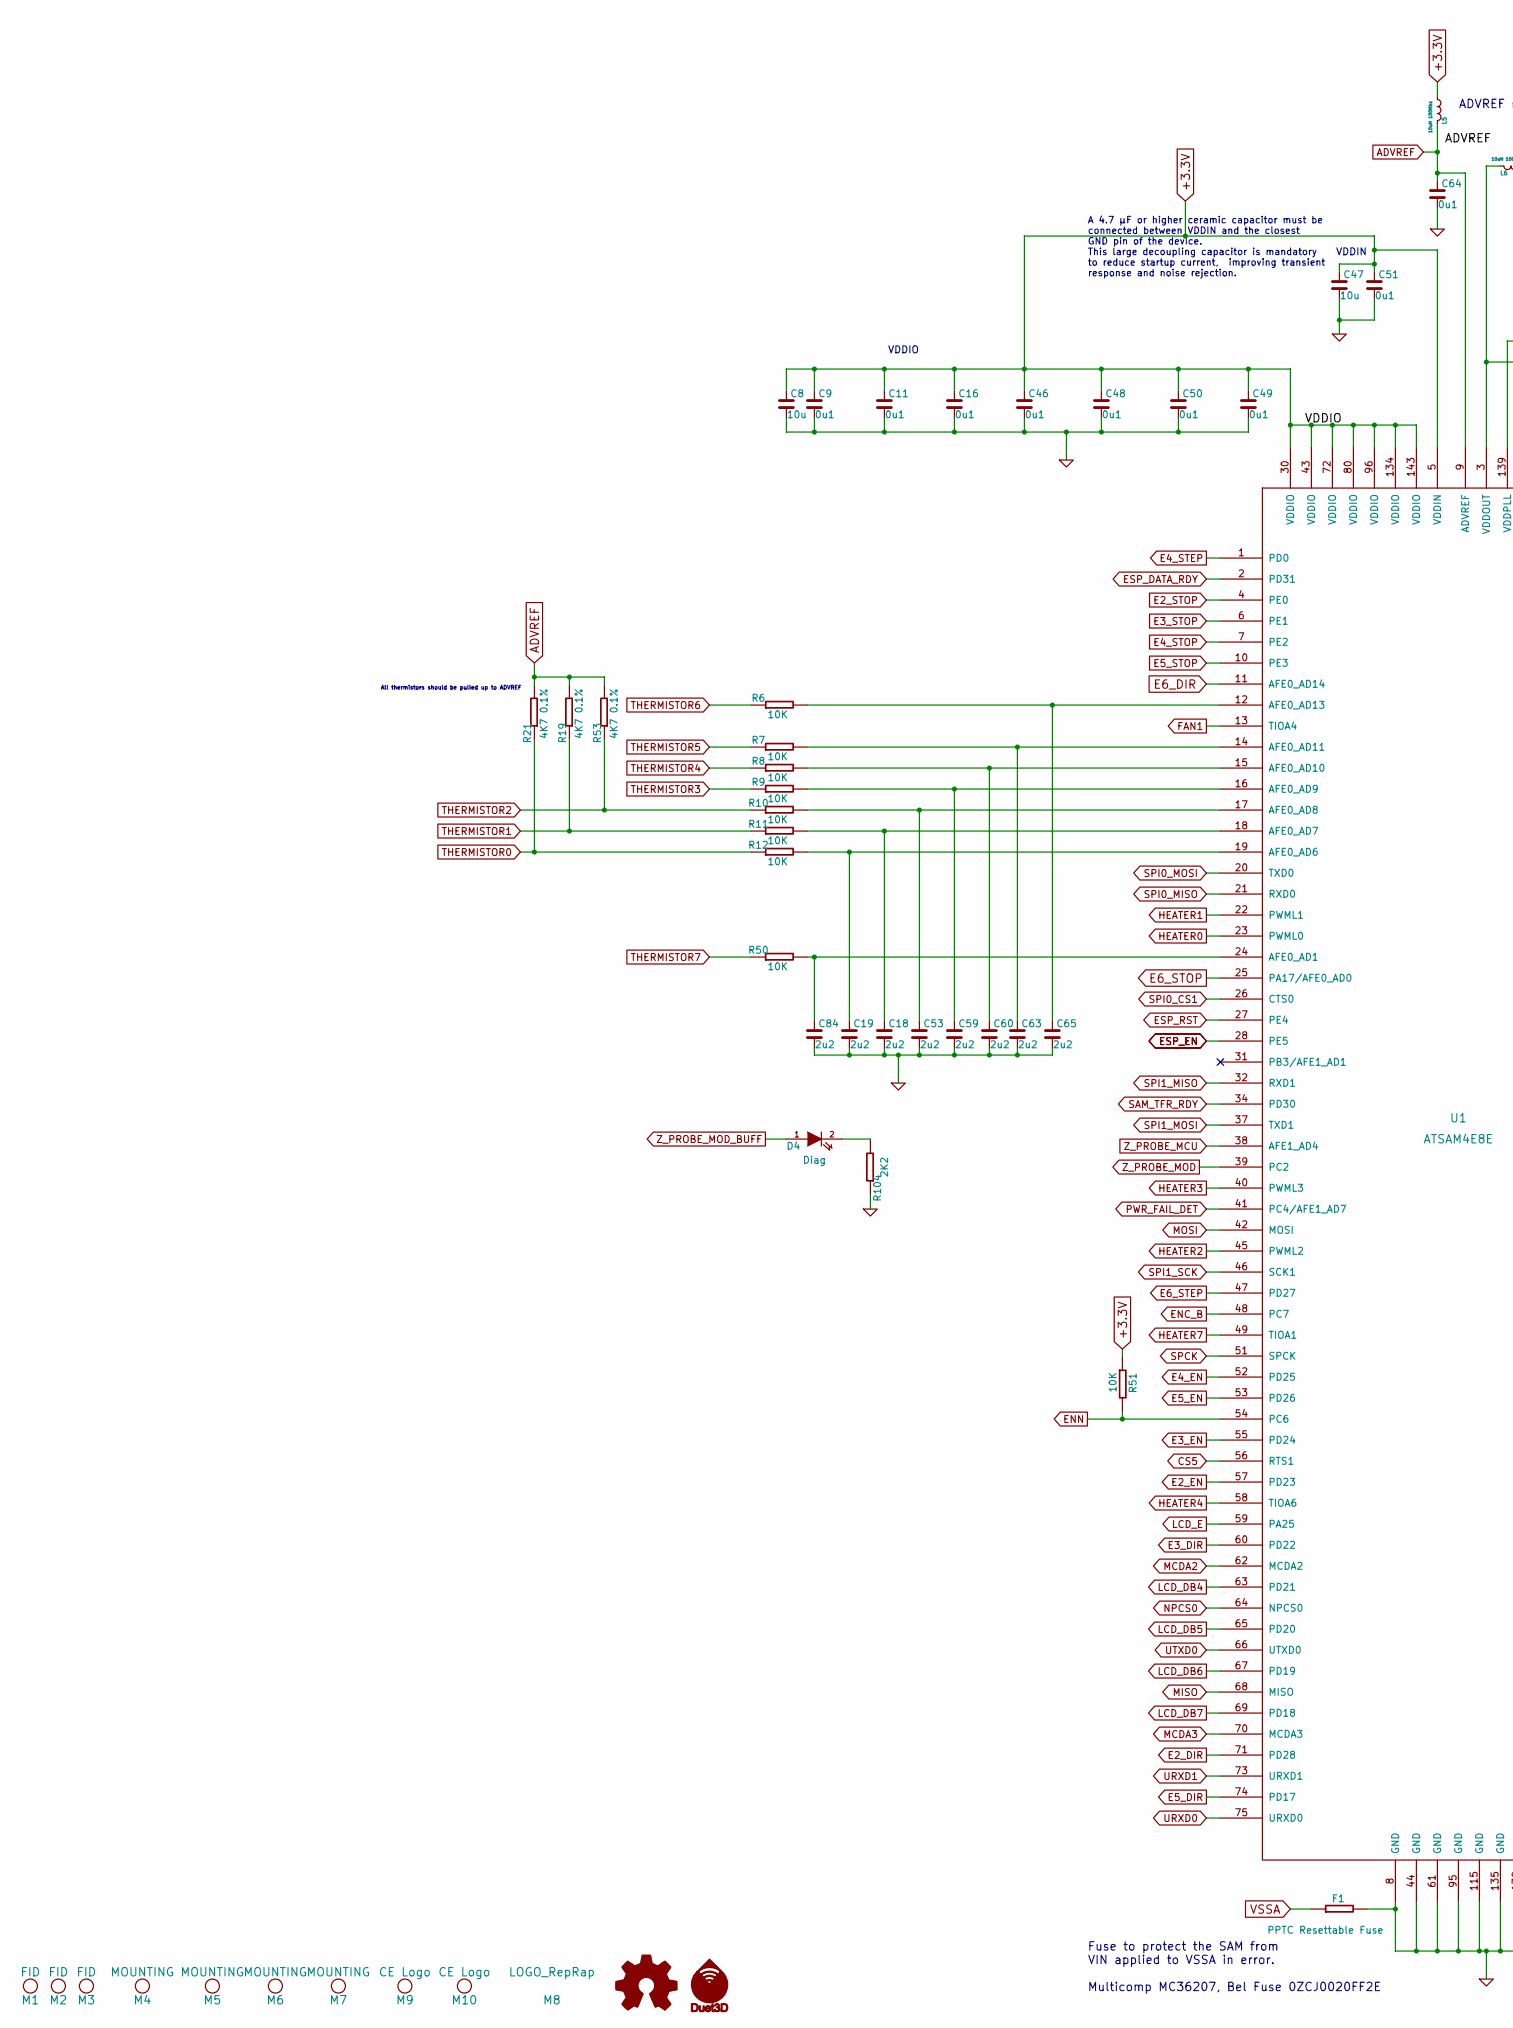
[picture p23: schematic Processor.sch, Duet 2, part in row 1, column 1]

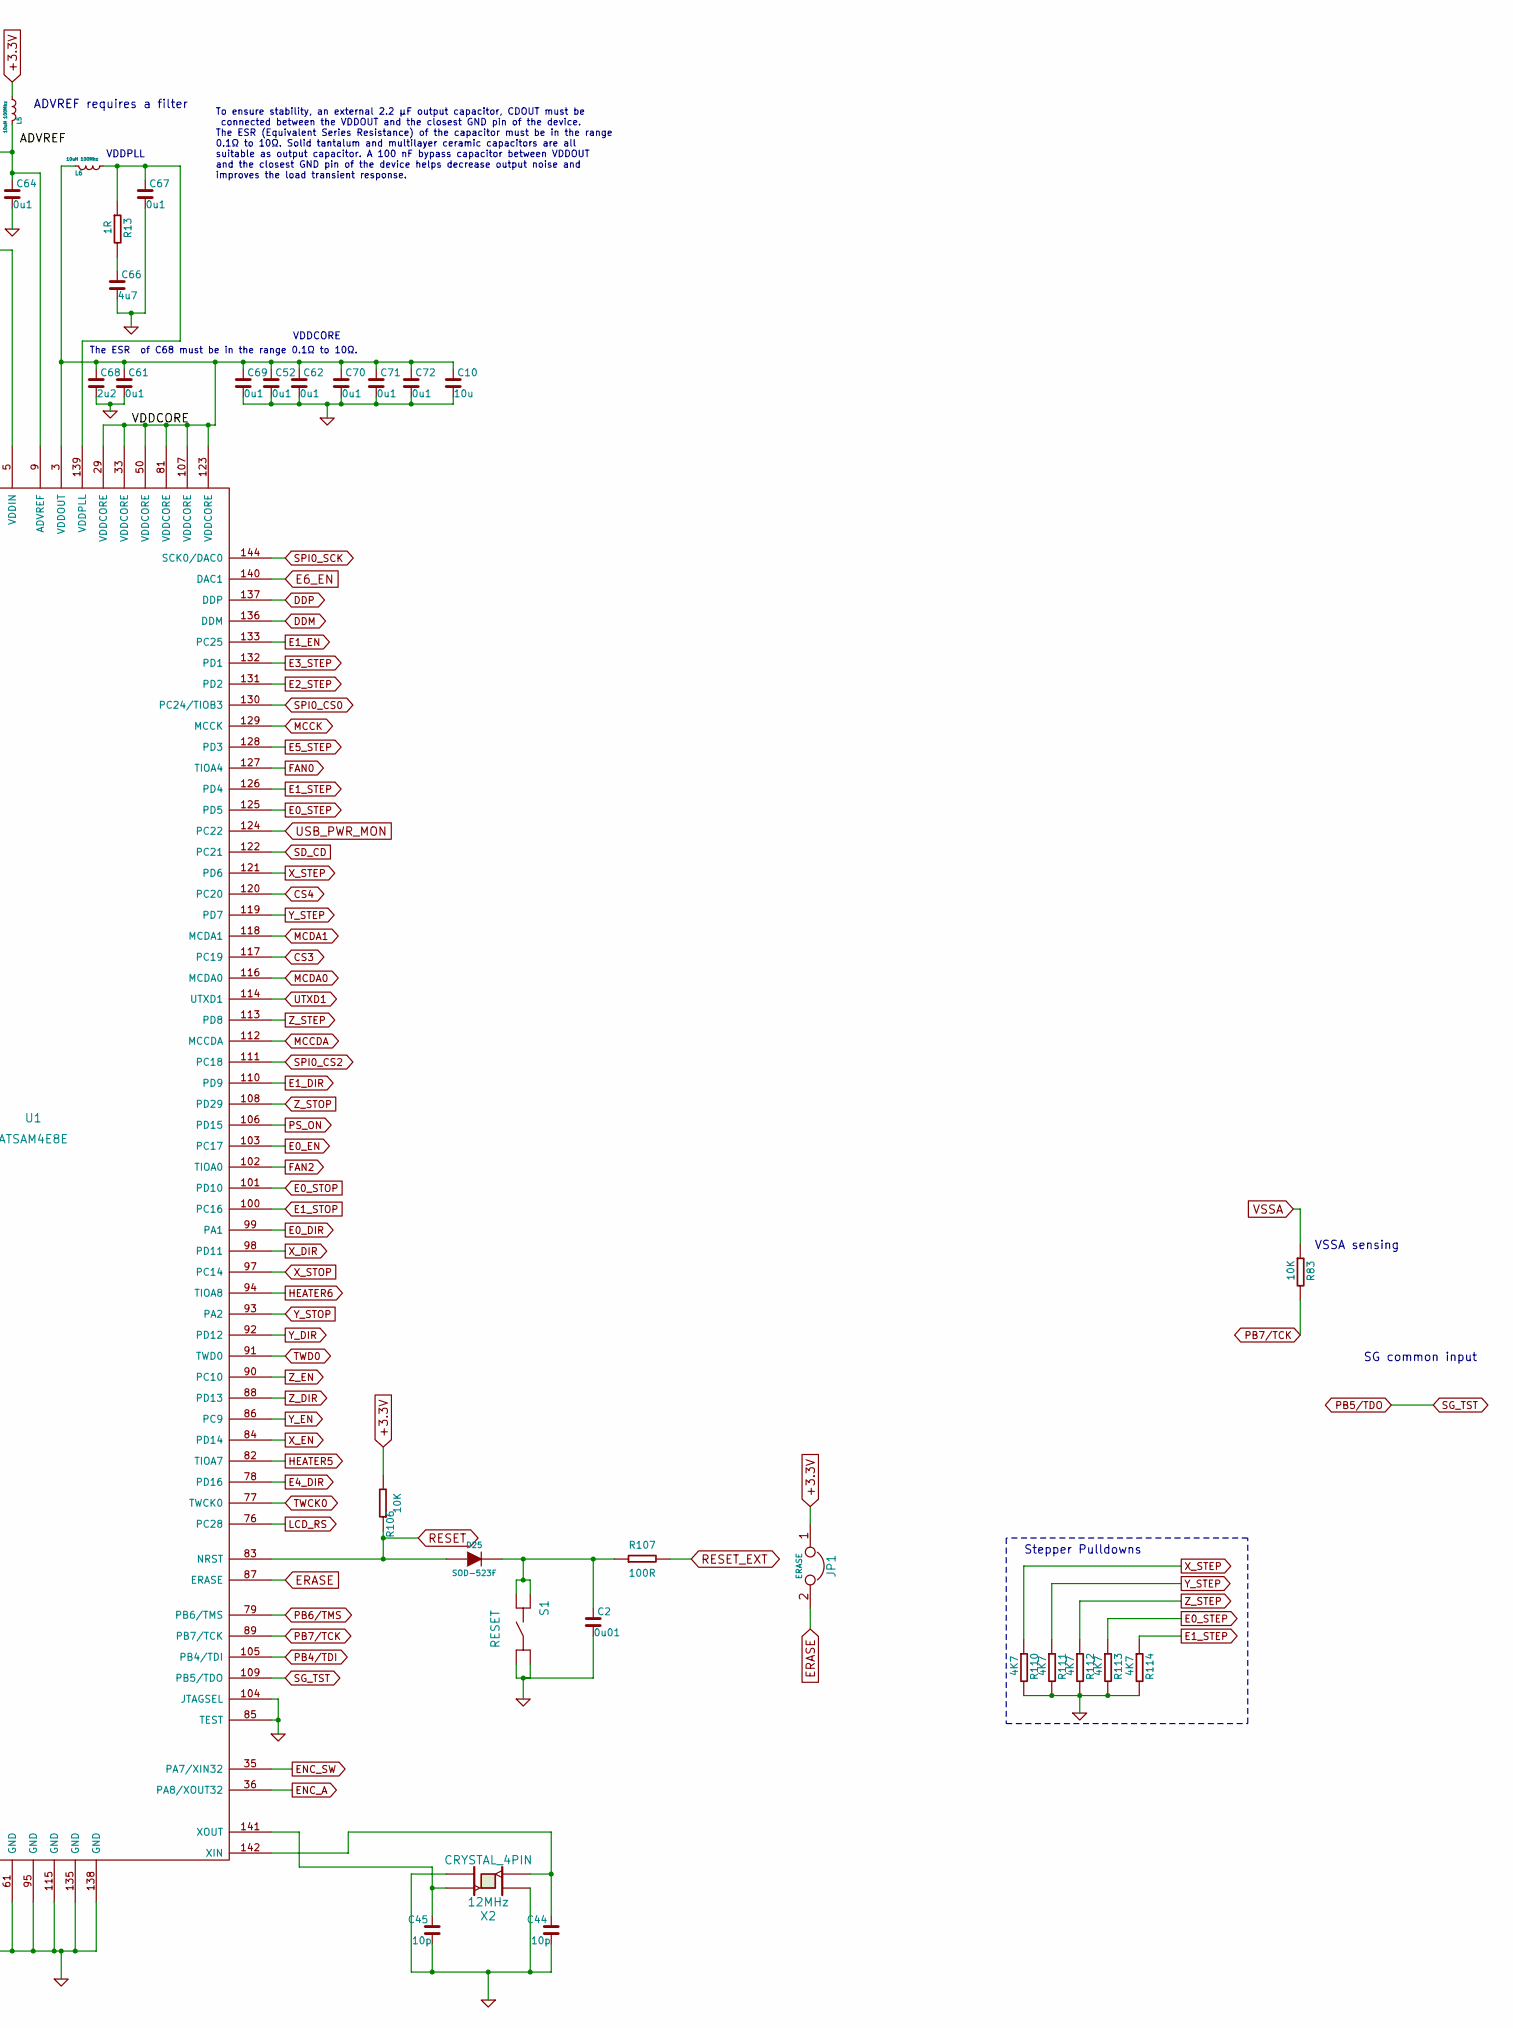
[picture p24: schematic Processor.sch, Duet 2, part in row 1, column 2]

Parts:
C2: 0u01; C_0603
C8, C10, C47: 10u; C_0805
C9, C11, C16, C46, C48, C49, C50, C51, C52, C61, C62, C64, C67, C69, C70, C71, C72: 0u1; C_0603
C18, C19, C53, C59, C60, C63, C65, C68, C84: 2u2; C_0603
C44, C45: 10p; C_0603
C66: 4u7; C_0805
D4: Diag; D_0603
D25: SOD-523F
F1: PPTC Resettable Fuse; R_1206
JP1: ERASE; JUMPER
L5, L6: 10uH 100Mhz; R_0603
M1, M2, M3: FID; Fiducial_1mm_Dia_2.54mm_Outer_CopperTop
M4, M5, M6, M7: MOUNTING; Fixing_M4
M8: LOGO_RepRap; Logo_RepRap
M9: CE Logo; Logo_CE_5mm
M10: CE Logo; Logo_CE_5mm_mirror
M11: Logo_Open_Hardware_Small; OSHW-Logo_11.4x12mm_SilkScreen
M12: Duet3D_Logo; Logo_Duet3D_vertical
R6, R7, R8, R9, R10, R11, R12, R50, R51, R83, R106: 10K; R_0603
R13: 1R; R_0603
R19, R21, R53: 4K7 0.1%; R_0603
R104: 2K2; R_0603
R107: 100R; R_0603
R110, R111, R112, R113, R114: 4K7; R_0603
S1: RESET; SW_SIDE_1_lugs
U1: ATSAM4E8E; LQFP144
X2: CRYSTAL_4PIN; Xtal_5x3.2

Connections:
+3.3V: C8.1, C9.1, C11.1, C16.1, C46.1, C47.1, C48.1, C49.1, C50.1, C51.1, JP1.1, L5.2 (B), R51.1, R106.2, U1.5 (VDDIN), U1.30 (VDDIO), U1.43 (VDDIO), U1.72 (VDDIO), U1.80 (VDDIO), U1.96 (VDDIO), U1.134 (VDDIO), U1.143 (VDDIO); also elsewhere on the board
/Processor/VDDCORE: C10.1, C52.1, C61.1, C62.1, C68.1, C69.1, C70.1, C71.1, C72.1, L6.1 (A), U1.3 (VDDOUT), U1.29 (VDDCORE), U1.33 (VDDCORE), U1.50 (VDDCORE), U1.81 (VDDCORE), U1.107 (VDDCORE), U1.123 (VDDCORE)
ADVREF: C64.1, L5.1 (A), R19.2, R21.2, R53.2, U1.9 (ADVREF); also elsewhere on the board
CS3: U1.117 (PC19); also elsewhere on the board
CS4: U1.120 (PC20); also elsewhere on the board
CS5: U1.56 (RTS1); also elsewhere on the board
DDM: U1.136 (DDM); also elsewhere on the board
DDP: U1.137 (DDP); also elsewhere on the board
E0_DIR: U1.99 (PA1); also elsewhere on the board
E0_EN: U1.103 (PC17); also elsewhere on the board
E0_STEP: R113.1, U1.125 (PD5); also elsewhere on the board
E0_STOP: U1.101 (PD10); also elsewhere on the board
E1_DIR: U1.110 (PD9); also elsewhere on the board
E1_EN: U1.133 (PC25); also elsewhere on the board
E1_STEP: R114.1, U1.126 (PD4); also elsewhere on the board
E1_STOP: U1.100 (PC16); also elsewhere on the board
E2_DIR: U1.71 (PD28); also elsewhere on the board
E2_EN: U1.57 (PD23); also elsewhere on the board
E2_STEP: U1.131 (PD2); also elsewhere on the board
E2_STOP: U1.4 (PE0); also elsewhere on the board
E3_DIR: U1.60 (PD22); also elsewhere on the board
E3_EN: U1.55 (PD24); also elsewhere on the board
E3_STEP: U1.132 (PD1); also elsewhere on the board
E3_STOP: U1.6 (PE1); also elsewhere on the board
E4_DIR: U1.78 (PD16); also elsewhere on the board
E4_EN: U1.52 (PD25); also elsewhere on the board
E4_STEP: U1.1 (PD0); also elsewhere on the board
E4_STOP: U1.7 (PE2); also elsewhere on the board
E5_DIR: U1.74 (PD17); also elsewhere on the board
E5_EN: U1.53 (PD26); also elsewhere on the board
E5_STEP: U1.128 (PD3); also elsewhere on the board
E5_STOP: U1.10 (PE3); also elsewhere on the board
E6_DIR: U1.11 (AFE0_AD14); also elsewhere on the board
E6_EN: U1.140 (DAC1); also elsewhere on the board
E6_STEP: U1.47 (PD27); also elsewhere on the board
E6_STOP: U1.25 (PA17/AFE0_AD0); also elsewhere on the board
ENC_A: U1.36 (PA8/XOUT32); also elsewhere on the board
ENC_B: U1.48 (PC7); also elsewhere on the board
ENC_SW: U1.35 (PA7/XIN32); also elsewhere on the board
ENN: R51.2, U1.54 (PC6); also elsewhere on the board
ERASE: JP1.2, U1.87 (ERASE)
ESP_DATA_RDY: U1.2 (PD31); also elsewhere on the board
ESP_EN: U1.28 (PE5); also elsewhere on the board
ESP_RST: U1.27 (PE4); also elsewhere on the board
FAN0: U1.127 (TIOA4); also elsewhere on the board
FAN1: U1.13 (TIOA4); also elsewhere on the board
FAN2: U1.102 (TIOA0); also elsewhere on the board
GND: C2.2, C8.2, C9.2, C10.2, C11.2, C16.2, C18.2, C19.2, C44.2, C45.2, C46.2, C47.2, C48.2, C49.2, C50.2, C51.2, C52.2, C53.2, C59.2, C60.2, C61.2, C62.2, C63.2, C64.2, C65.2, C66.2, C67.2, C68.2, C69.2, C70.2, C71.2, C72.2, C84.2, F1.2, R104.1, R110.2, R111.2, R112.2, R113.2, R114.2, S1.1, S1.2, U1.8 (GND), U1.44 (GND), U1.61 (GND), U1.85 (TEST), U1.95 (GND), U1.104 (JTAGSEL), U1.115 (GND), U1.135 (GND), U1.138 (GND), X2.2, X2.4; also elsewhere on the board
HEATER0: U1.23 (PWML0); also elsewhere on the board
HEATER1: U1.22 (PWML1); also elsewhere on the board
HEATER2: U1.45 (PWML2); also elsewhere on the board
HEATER3: U1.40 (PWML3); also elsewhere on the board
HEATER4: U1.58 (TIOA6); also elsewhere on the board
HEATER5: U1.82 (TIOA7); also elsewhere on the board
HEATER6: U1.94 (TIOA8); also elsewhere on the board
HEATER7: U1.49 (TIOA1); also elsewhere on the board
LCD_DB4: U1.63 (PD21); also elsewhere on the board
LCD_DB5: U1.65 (PD20); also elsewhere on the board
LCD_DB6: U1.67 (PD19); also elsewhere on the board
LCD_DB7: U1.69 (PD18); also elsewhere on the board
LCD_E: U1.59 (PA25); also elsewhere on the board
LCD_RS: U1.76 (PC28); also elsewhere on the board
MCCDA: U1.112 (MCCDA); also elsewhere on the board
MCCK: U1.129 (MCCK); also elsewhere on the board
MCDA0: U1.116 (MCDA0); also elsewhere on the board
MCDA1: U1.118 (MCDA1); also elsewhere on the board
MCDA2: U1.62 (MCDA2); also elsewhere on the board
MCDA3: U1.70 (MCDA3); also elsewhere on the board
MISO: U1.68 (MISO); also elsewhere on the board
MOSI: U1.42 (MOSI); also elsewhere on the board
NPCS0: U1.64 (NPCS0); also elsewhere on the board
unnamed: C2.1, D25.1 (K), R107.1, S1.3, S1.4
unnamed: C18.1, R11.2, U1.18 (AFE0_AD7)
unnamed: C19.1, R12.2, U1.19 (AFE0_AD6)
unnamed: C44.1, U1.142 (XIN), X2.3
unnamed: C45.1, U1.141 (XOUT), X2.1
unnamed: C53.1, R10.2, U1.17 (AFE0_AD8)
unnamed: C59.1, R9.2, U1.16 (AFE0_AD9)
unnamed: C60.1, R8.2, U1.15 (AFE0_AD10)
unnamed: C63.1, R7.2, U1.14 (AFE0_AD11)
unnamed: C65.1, R6.2, U1.12 (AFE0_AD13)
unnamed: C66.1, R13.2
unnamed: C67.1, L6.2 (B), R13.1, U1.139 (VDDPLL)
unnamed: C84.1, R50.2, U1.24 (AFE0_AD1)
unnamed: D4.2 (K), R104.2
PB4/TDI: U1.105 (PB4/TDI)
PB5/TDO: U1.109 (PB5/TDO); also elsewhere on the board
PB6/TMS: U1.79 (PB6/TMS); also elsewhere on the board
PB7/TCK: R83.2, U1.89 (PB7/TCK)
PS_ON: U1.106 (PD15); also elsewhere on the board
PWR_FAIL_DET: U1.41 (PC4/AFE1_AD7); also elsewhere on the board
RESET: D25.2 (A), R106.1, U1.83 (NRST)
RESET_EXT: R107.2; also elsewhere on the board
SAM_TFR_RDY: U1.34 (PD30); also elsewhere on the board
SD_CD: U1.122 (PC21); also elsewhere on the board
SPCK: U1.51 (SPCK); also elsewhere on the board
SPI0_CS0: U1.130 (PC24/TIOB3); also elsewhere on the board
SPI0_CS1: U1.26 (CTS0); also elsewhere on the board
SPI0_CS2: U1.111 (PC18); also elsewhere on the board
SPI0_MISO: U1.21 (RXD0); also elsewhere on the board
SPI0_MOSI: U1.20 (TXD0); also elsewhere on the board
SPI0_SCK: U1.144 (SCK0/DAC0); also elsewhere on the board
SPI1_MISO: U1.32 (RXD1); also elsewhere on the board
SPI1_MOSI: U1.37 (TXD1); also elsewhere on the board
SPI1_SCK: U1.46 (SCK1); also elsewhere on the board
THERMISTOR0: R12.1, R21.1; also elsewhere on the board
THERMISTOR1: R11.1, R19.1; also elsewhere on the board
THERMISTOR2: R10.1, R53.1; also elsewhere on the board
THERMISTOR3: R9.1; also elsewhere on the board
THERMISTOR4: R8.1; also elsewhere on the board
THERMISTOR5: R7.1; also elsewhere on the board
THERMISTOR6: R6.1; also elsewhere on the board
THERMISTOR7: R50.1; also elsewhere on the board
TWCK0: U1.77 (TWCK0); also elsewhere on the board
TWD0: U1.91 (TWD0); also elsewhere on the board
URXD0: U1.75 (URXD0); also elsewhere on the board
URXD1: U1.73 (URXD1); also elsewhere on the board
USB_PWR_MON: U1.124 (PC22); also elsewhere on the board
UTXD0: U1.66 (UTXD0); also elsewhere on the board
UTXD1: U1.114 (UTXD1); also elsewhere on the board
VSSA: F1.1, R83.1; also elsewhere on the board
X_DIR: U1.98 (PD11); also elsewhere on the board
X_EN: U1.84 (PD14); also elsewhere on the board
X_STEP: R110.1, U1.121 (PD6); also elsewhere on the board
X_STOP: U1.97 (PC14); also elsewhere on the board
Y_DIR: U1.92 (PD12); also elsewhere on the board
Y_EN: U1.86 (PC9); also elsewhere on the board
Y_STEP: R111.1, U1.119 (PD7); also elsewhere on the board
Y_STOP: U1.93 (PA2); also elsewhere on the board
Z_DIR: U1.88 (PD13); also elsewhere on the board
Z_EN: U1.90 (PC10); also elsewhere on the board
Z_PROBE_MCU: U1.38 (AFE1_AD4); also elsewhere on the board
Z_PROBE_MOD: U1.39 (PC2); also elsewhere on the board
Z_PROBE_MOD_BUFF: D4.1 (A); also elsewhere on the board
Z_STEP: R112.1, U1.113 (PD8); also elsewhere on the board
Z_STOP: U1.108 (PD29); also elsewhere on the board

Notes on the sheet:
VDDPLL
VDDCORE
VDDIO
VDDIN
A 4.7 μF or higher ceramic capacitor must be connected between VDDIN and the closest GND pin of the device. This large decoupling capacitor is mandatory to reduce startup current, improving transient response and noise rejection.
To ensure stability, an external 2.2 μF output capacitor, CDOUT must be connected between the VDDOUT and the closest GND pin of the device. The ESR (Equivalent Series Resistance) of the capacitor must be in the range 0.1Ω to 10Ω. Solid tantalum and multilayer ceramic capacitors are all suitable as 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
Fuse to protect the SAM from VIN applied to VSSA in error. Multicomp MC36207, Bel Fuse 0ZCJ0020FF2E
The ESR of C68 must be in the range 0.1Ω to 10Ω.
All thermistors should be pulled up to ADVREF
ADVREF requires a filter
VSSA sensing
SG common input
Stepper Pulldowns

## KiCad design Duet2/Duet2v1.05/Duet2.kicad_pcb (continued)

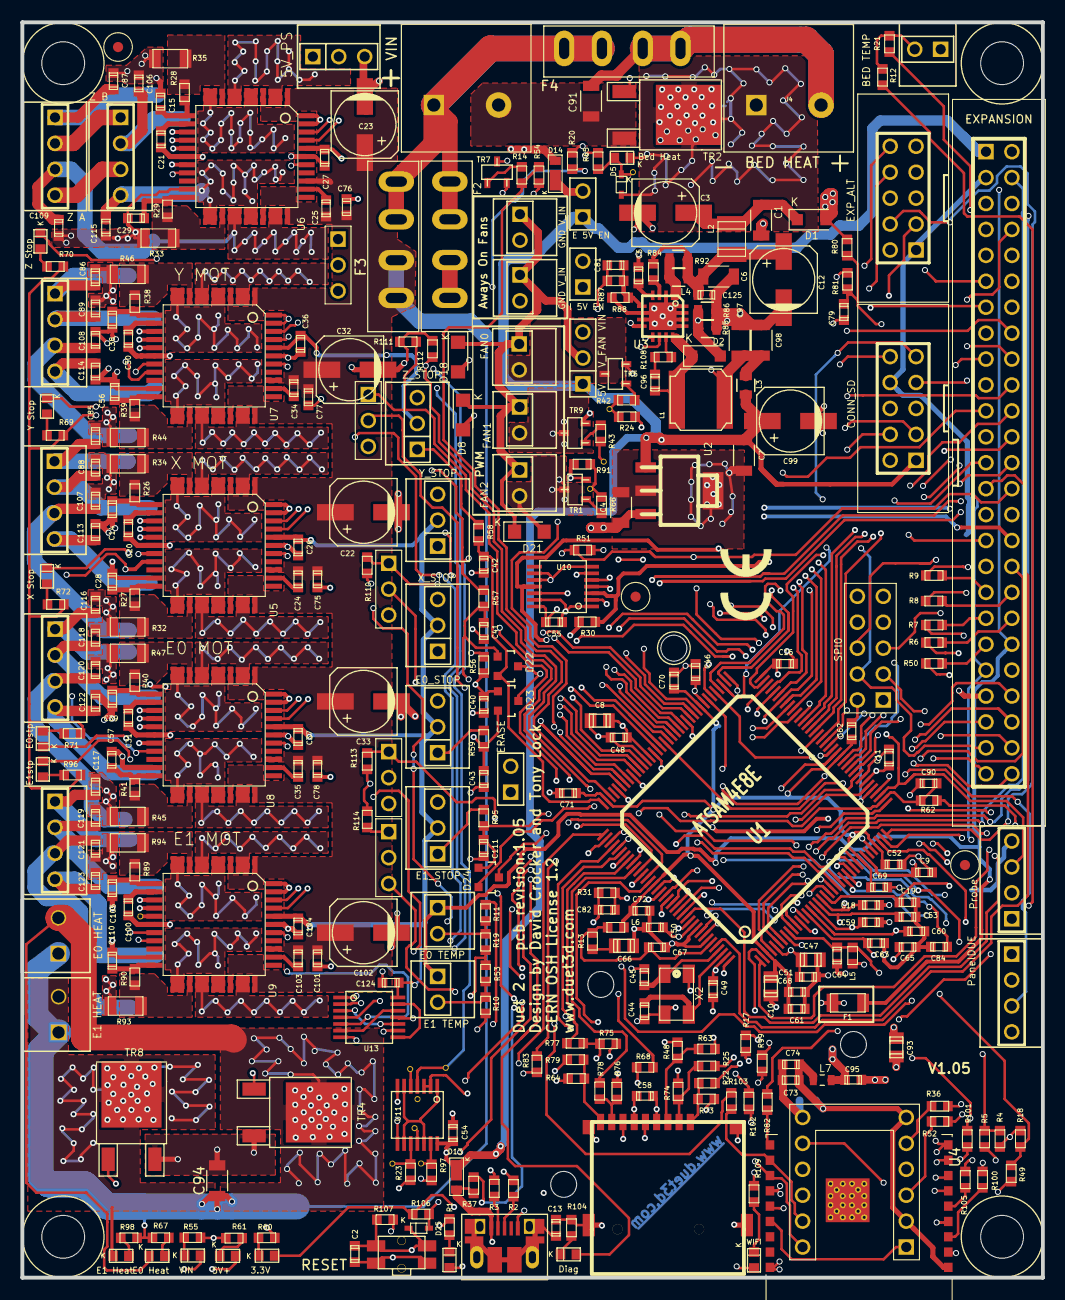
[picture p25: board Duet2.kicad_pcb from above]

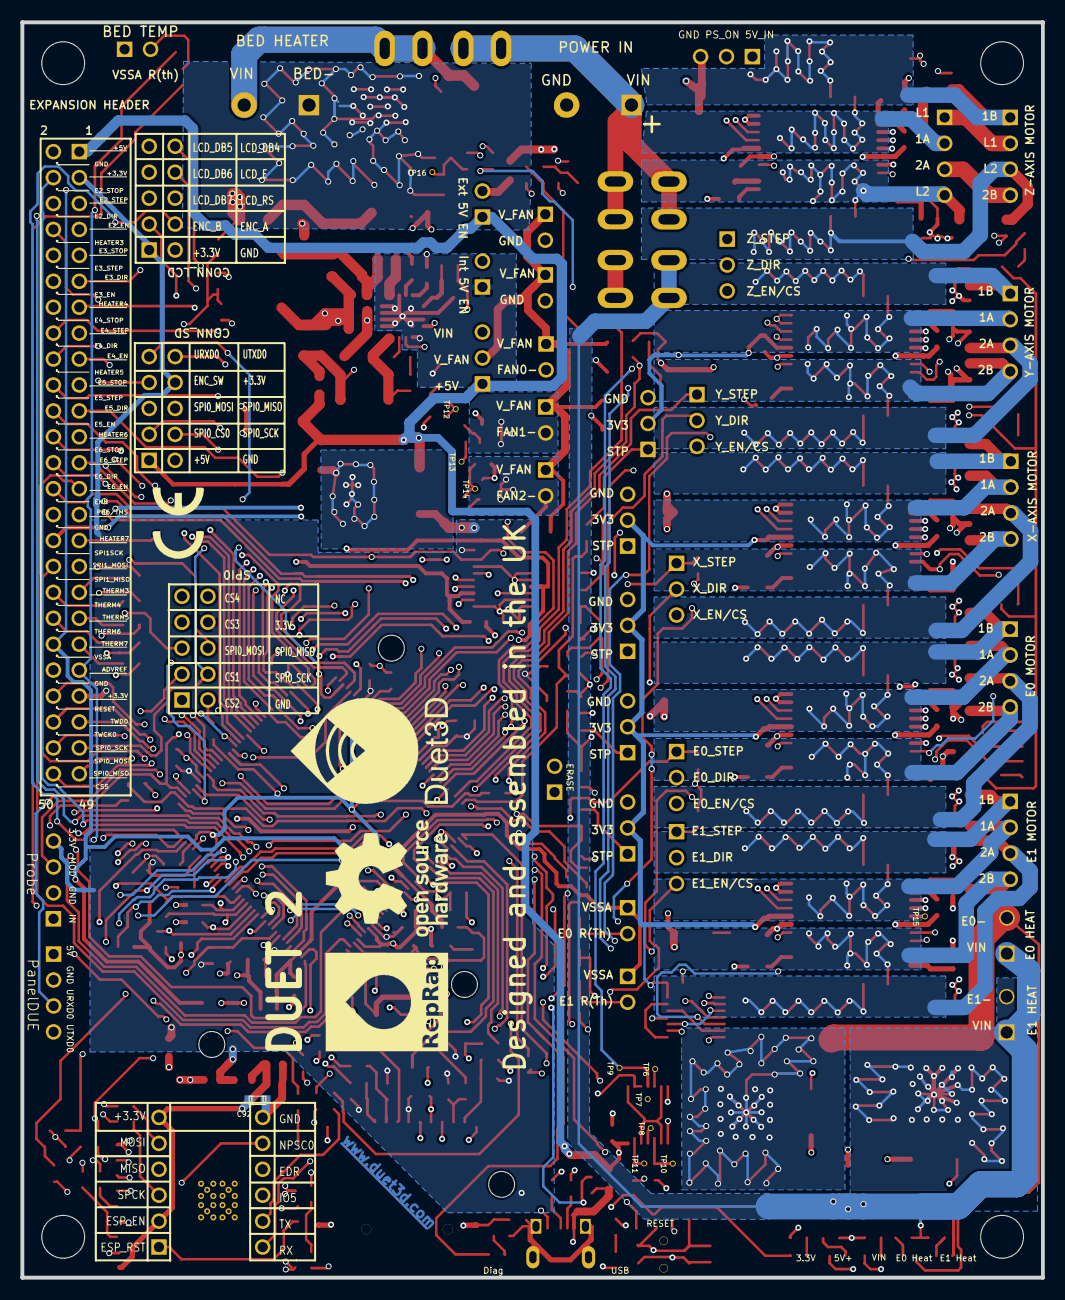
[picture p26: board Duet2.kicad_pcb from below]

Board: 4 copper layers, 100.0 x 123.0 mm, 356 parts (5 on the bottom side), 281 nets.

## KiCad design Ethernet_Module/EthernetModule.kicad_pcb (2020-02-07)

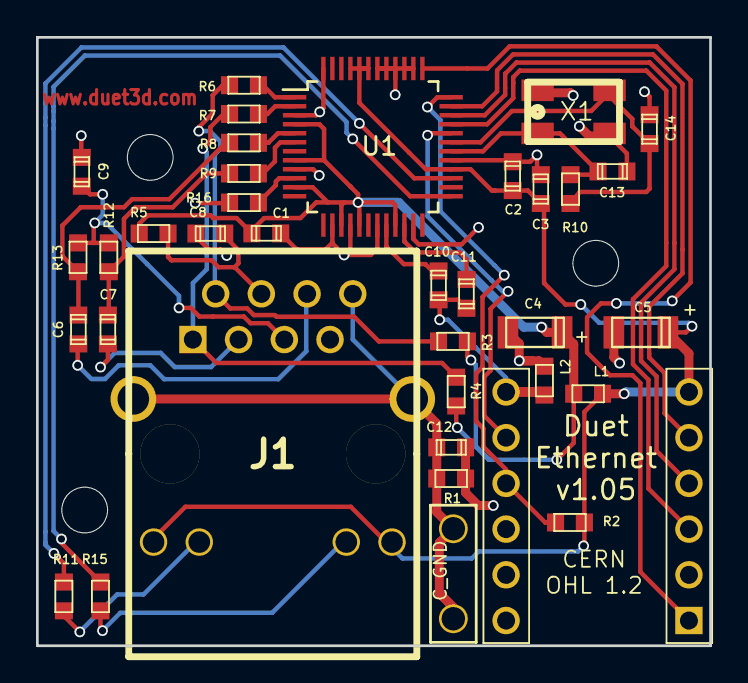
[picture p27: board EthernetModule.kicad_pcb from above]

Board: 2 copper layers, 37.4 x 33.8 mm, 36 parts (0 on the bottom side), 32 nets.

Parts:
C1, C2, C3: 0u1; C_0603
C4, C5: 10uF/16V; C_1206_pol
C6, C7: 6n8; C_0603
C8: 22n; C_0603
C9, C11: 10n; C_0603
C10: 4u7; C_0603
C12: 0u01 +200V; C_0603
C13, C14: 18p; C_0603
J1: RJ45+MAG
J2: CONN_ALT_HEADER; CONN_ALT_HEADER_th
J3: C_GND; 2.8mm_Spade_terminal
L1, L2: L_MINI; R_0603
R1, R10: 1M; R_0603
R2: 4K7; R_0603
R3, R4, R12, R13: 49R9; R_0603
R5: 10R; R_0603
R6, R7, R8, R9: 33R; R_0603
R11, R15: 220R; R_0603
R16: 12K4; R_0603
U1: W5500; LQFP-48_7x7mm_Pitch0.5mm
X1: CRYSTAL_4PIN; Xtal_5x3.2

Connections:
+3V3: C2.1, C3.1, C5.1, J1.9, J1.12, J2.6, L1.2, R2.2, U1.28, U1.43, U1.44, U1.45
+3V3_A: C1.1, C4.1, L1.1, R3.2, R4.2, R5.2, U1.4, U1.8, U1.11, U1.15, U1.17, U1.21
ACTLED: R11.2, U1.27
AGND: C1.2, C4.2, C8.2, C9.2, L2.1, R16.1, U1.3, U1.9, U1.14, U1.16, U1.19, U1.48
GND: C2.2, C3.2, C5.2, C10.2, C11.2, C12.1, C13.2, C14.2, J2.10, J2.15, L2.2, R1.1, U1.23, U1.29, U1.38, U1.39, U1.40, U1.41, U1.42, X1.2, X1.4
INTn: J2.12, R2.1, U1.36
LINKLED: R15.2, U1.25
MISO: J2.4, U1.34
MOSI: J2.5, U1.35
unnamed: C6.1, R8.1, R13.2
unnamed: C6.2, J1.6
unnamed: C7.1, R9.1, R12.2
unnamed: C7.2, J1.3
unnamed: C8.1, J1.4, R5.1
unnamed: C9.1, J1.5, R12.1, R13.1
unnamed: C10.1, U1.20
unnamed: C11.1, U1.22
unnamed: C12.2, J1.8, J1.13, J1.14, J3.1, R1.2
unnamed: C13.1, R10.2, U1.30, X1.1
unnamed: C14.1, R10.1, U1.31, X1.3
unnamed: J1.1, R4.1, R7.1
unnamed: J1.2, R3.1, R6.1
unnamed: J1.10, R11.1
unnamed: J1.11, R15.1
unnamed: R6.2, U1.1
unnamed: R7.2, U1.2
unnamed: R8.2, U1.5
unnamed: R9.2, U1.6
unnamed: R16.2, U1.10
RSTn: J2.1, U1.37
SCLK: J2.3, U1.33
SCSn: J2.11, U1.32

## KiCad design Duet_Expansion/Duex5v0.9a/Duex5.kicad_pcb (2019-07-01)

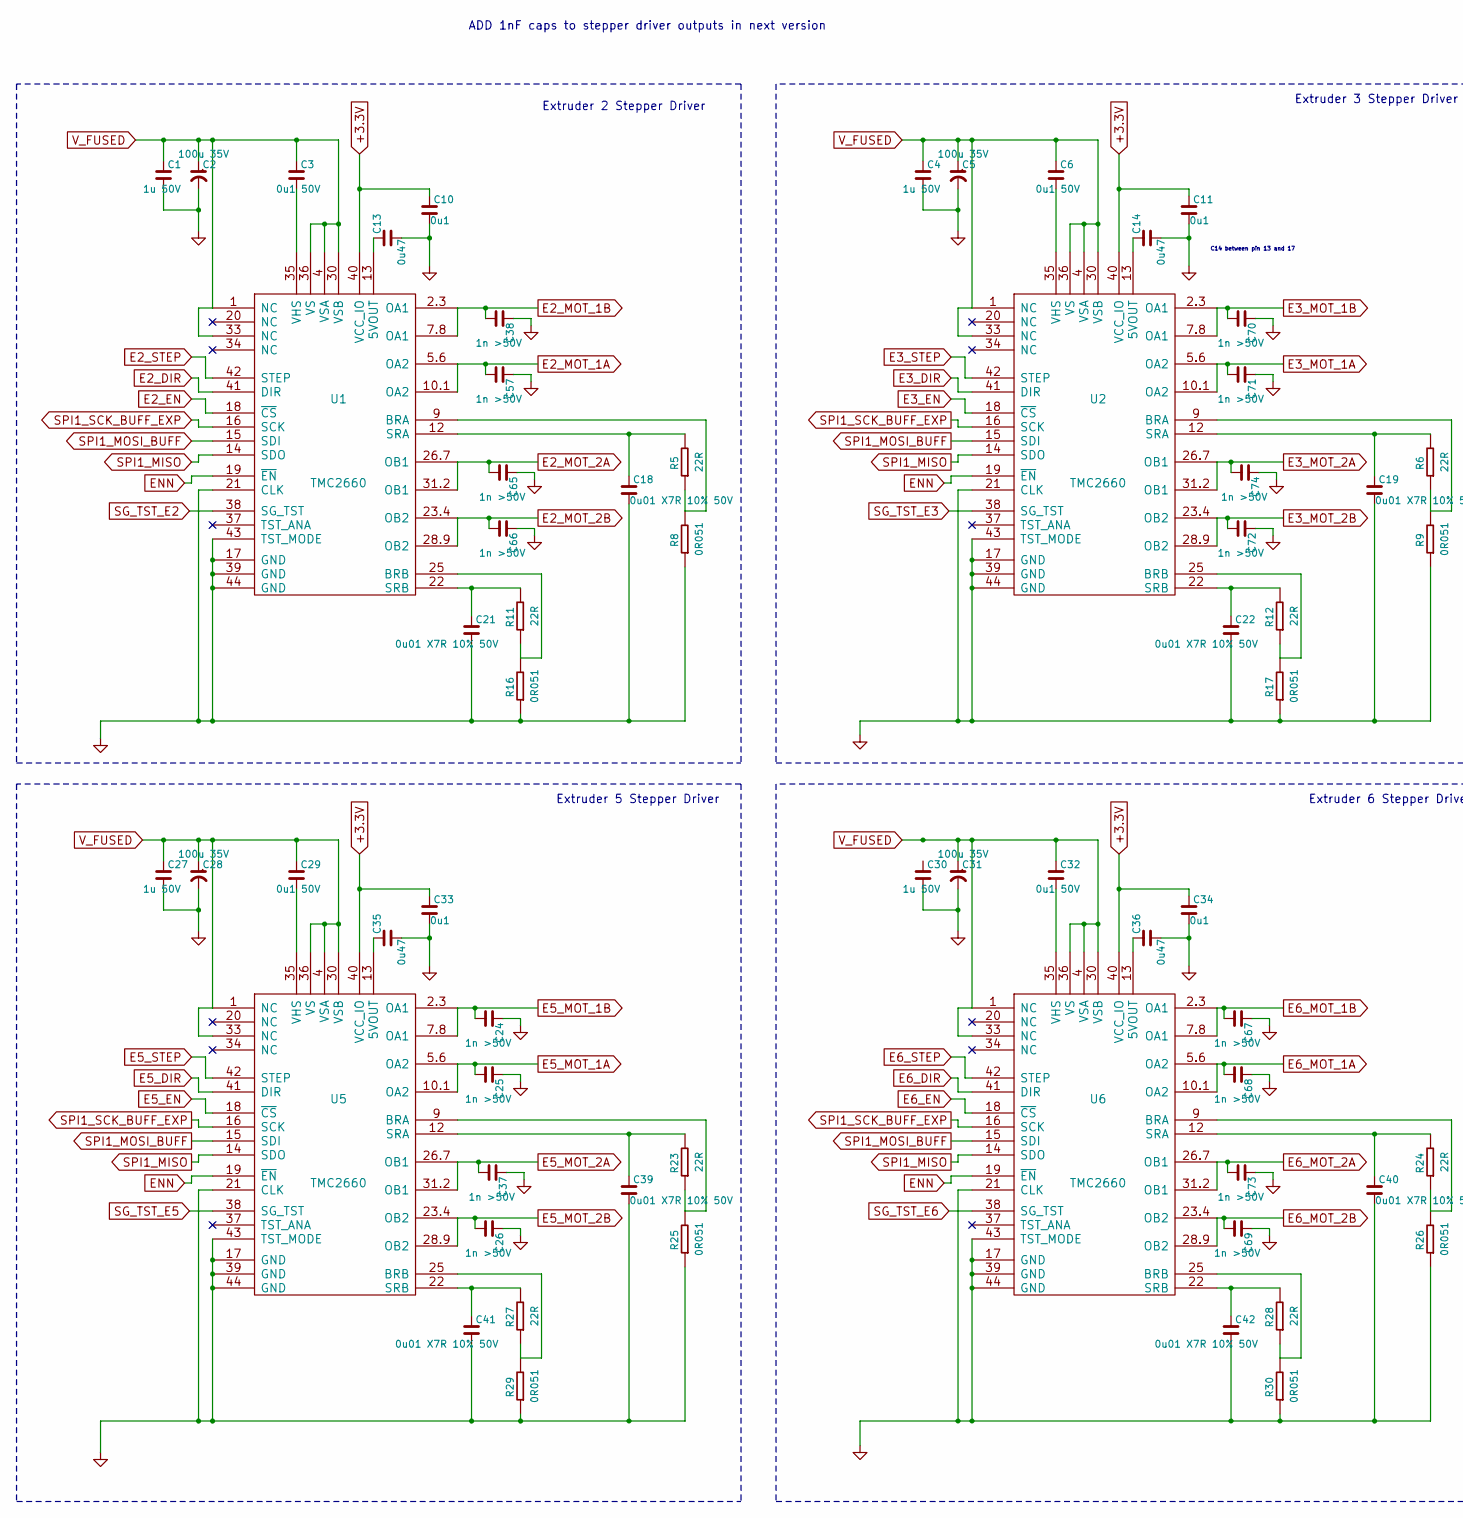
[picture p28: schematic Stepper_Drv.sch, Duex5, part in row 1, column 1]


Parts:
C1, C4, C7, C27, C30: 1u 50V; C_0603
C2, C5, C8, C28, C31: 100u 35V; C_ELEC_6.3x7.7
C3, C6, C9, C29, C32: 0u1 50V; C_0603
C10, C11, C12, C33, C34, C53: 0u1; C_0603
C13, C14, C15, C35, C36: 0u47; C_0603
C18, C19, C20, C21, C22, C23, C39, C40, C41, C42: 0u01 X7R 10% 50V; C_0603
C24, C25, C26, C37, C38, C57, C65, C66, C67, C68, C69, C70, C71, C72, C73, C74, C75, C76, C77, C78: 1n >50V; C_0603
D1: E2stp; D_0603
D2: E3stp; D_0603
D3: E4stp; D_0603
D4: E5stp; D_0603
D5: E6stp; D_0603
R1, R2, R14, R15, R21: 1K; R_0603
R4, R19, R20: 0R; R_0603
R5, R6, R7, R11, R12, R13, R23, R24, R27, R28: 22R; R_0603
R8, R9, R10, R16, R17, R18, R25, R26, R29, R30: 0R051; R_1206
U1, U2, U3, U5, U6: TMC2660
U12: 74HC32; TSSOP-14

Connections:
+3.3V: C10.1, C11.1, C12.1, C33.1, C34.1, C53.1, U1.40 (VCC_IO), U2.40 (VCC_IO), U3.40 (VCC_IO), U5.40 (VCC_IO), U6.40 (VCC_IO), U12.14 (VCC); also elsewhere on the board
E2_DIR: U1.41 (DIR); also elsewhere on the board
E2_EN: U1.18 (~CS); also elsewhere on the board
E2_MOT_1A: C57.2, U1.5.6 (OA2), U1.10.1 (OA2); also elsewhere on the board
E2_MOT_1B: C38.2, U1.2.3 (OA1), U1.7.8 (OA1); also elsewhere on the board
E2_MOT_2A: C65.2, U1.26.7 (OB1), U1.31.2 (OB1); also elsewhere on the board
E2_MOT_2B: C66.2, U1.23.4 (OB2), U1.28.9 (OB2); also elsewhere on the board
E2_STEP: U1.42 (STEP); also elsewhere on the board
E2_STOP: D1.2 (K); also elsewhere on the board
E3_DIR: U2.41 (DIR); also elsewhere on the board
E3_EN: U2.18 (~CS); also elsewhere on the board
E3_MOT_1A: C71.2, U2.5.6 (OA2), U2.10.1 (OA2); also elsewhere on the board
E3_MOT_1B: C70.2, U2.2.3 (OA1), U2.7.8 (OA1); also elsewhere on the board
E3_MOT_2A: C74.2, U2.26.7 (OB1), U2.31.2 (OB1); also elsewhere on the board
E3_MOT_2B: C72.2, U2.23.4 (OB2), U2.28.9 (OB2); also elsewhere on the board
E3_STEP: U2.42 (STEP); also elsewhere on the board
E3_STOP: D2.2 (K); also elsewhere on the board
E4_DIR: U3.41 (DIR); also elsewhere on the board
E4_EN: U3.18 (~CS); also elsewhere on the board
E4_MOT_1A: C76.2, U3.5.6 (OA2), U3.10.1 (OA2); also elsewhere on the board
E4_MOT_1B: C75.2, U3.2.3 (OA1), U3.7.8 (OA1); also elsewhere on the board
E4_MOT_2A: C78.2, U3.26.7 (OB1), U3.31.2 (OB1); also elsewhere on the board
E4_MOT_2B: C77.2, U3.23.4 (OB2), U3.28.9 (OB2); also elsewhere on the board
E4_STEP: U3.42 (STEP); also elsewhere on the board
E4_STOP: D3.2 (K); also elsewhere on the board
E5_DIR: U5.41 (DIR); also elsewhere on the board
E5_EN: U5.18 (~CS); also elsewhere on the board
E5_MOT_1A: C25.2, U5.5.6 (OA2), U5.10.1 (OA2); also elsewhere on the board
E5_MOT_1B: C24.2, U5.2.3 (OA1), U5.7.8 (OA1); also elsewhere on the board
E5_MOT_2A: C37.2, U5.26.7 (OB1), U5.31.2 (OB1); also elsewhere on the board
E5_MOT_2B: C26.2, U5.23.4 (OB2), U5.28.9 (OB2); also elsewhere on the board
E5_STEP: U5.42 (STEP); also elsewhere on the board
E5_STOP: D4.2 (K); also elsewhere on the board
E6_DIR: U6.41 (DIR); also elsewhere on the board
E6_EN: U6.18 (~CS); also elsewhere on the board
E6_MOT_1A: C68.2, U6.5.6 (OA2), U6.10.1 (OA2); also elsewhere on the board
E6_MOT_1B: C67.2, U6.2.3 (OA1), U6.7.8 (OA1); also elsewhere on the board
E6_MOT_2A: C73.2, U6.26.7 (OB1), U6.31.2 (OB1); also elsewhere on the board
E6_MOT_2B: C69.2, U6.23.4 (OB2), U6.28.9 (OB2); also elsewhere on the board
E6_STEP: U6.42 (STEP); also elsewhere on the board
E6_STOP: D5.2 (K); also elsewhere on the board
ENN: U1.19 (~EN), U2.19 (~EN), U3.19 (~EN), U5.19 (~EN), U6.19 (~EN); also elsewhere on the board
ES_V: R1.2, R2.2, R14.2, R15.2, R21.2; also elsewhere on the board
GND: C1.2, C2.2, C4.2, C5.2, C7.2, C8.2, C10.2, C11.2, C12.2, C13.2, C14.2, C15.2, C18.2, C19.2, C20.2, C21.2, C22.2, C23.2, C24.1, C25.1, C26.1, C27.2, C28.2, C30.2, C31.2, C33.2, C34.2, C35.2, C36.2, C37.1, C38.1, C39.2, C40.2, C41.2, C42.2, C53.2, C57.1, C65.1, C66.1, C67.1, C68.1, C69.1, C70.1, C71.1, C72.1, C73.1, C74.1, C75.1, C76.1, C77.1, C78.1, R4.1, R8.1, R9.1, R10.1, R16.1, R17.1, R18.1, R19.1, R20.1, R25.1, R26.1, R29.1, R30.1, U1.17 (GND), U1.21 (CLK), U1.39 (GND), U1.43 (TST_MODE), U1.44 (GND), U2.17 (GND), U2.21 (CLK), U2.39 (GND), U2.43 (TST_MODE), U2.44 (GND), U3.17 (GND), U3.21 (CLK), U3.39 (GND), U3.43 (TST_MODE), U3.44 (GND), U5.17 (GND), U5.21 (CLK), U5.39 (GND), U5.43 (TST_MODE), U5.44 (GND), U6.17 (GND), U6.21 (CLK), U6.39 (GND), U6.43 (TST_MODE), U6.44 (GND), U12.7 (GND); also elsewhere on the board
unnamed: C3.2, U1.35 (VHS)
unnamed: C6.2, U2.35 (VHS)
unnamed: C9.2, U3.35 (VHS)
unnamed: C13.1, U1.13 (5VOUT)
unnamed: C14.1, U2.13 (5VOUT)
unnamed: C15.1, U3.13 (5VOUT)
unnamed: C18.1, R5.2, U1.12 (SRA)
unnamed: C19.1, R6.2, U2.12 (SRA)
unnamed: C20.1, R7.2, U3.12 (SRA)
unnamed: C21.1, R11.2, U1.22 (SRB)
unnamed: C22.1, R12.2, U2.22 (SRB)
unnamed: C23.1, R13.2, U3.22 (SRB)
unnamed: C29.2, U5.35 (VHS)
unnamed: C32.2, U6.35 (VHS)
unnamed: C35.1, U5.13 (5VOUT)
unnamed: C36.1, U6.13 (5VOUT)
unnamed: C39.1, R23.2, U5.12 (SRA)
unnamed: C40.1, R24.2, U6.12 (SRA)
unnamed: C41.1, R27.2, U5.22 (SRB)
unnamed: C42.1, R28.2, U6.22 (SRB)
unnamed: D1.1 (A), R1.1
unnamed: D2.1 (A), R2.1
unnamed: D3.1 (A), R14.1
unnamed: D4.1 (A), R15.1
unnamed: D5.1 (A), R21.1
unnamed: R5.1, R8.2, U1.9 (BRA)
unnamed: R6.1, R9.2, U2.9 (BRA)
unnamed: R7.1, R10.2, U3.9 (BRA)
unnamed: R11.1, R16.2, U1.25 (BRB)
unnamed: R12.1, R17.2, U2.25 (BRB)
unnamed: R13.1, R18.2, U3.25 (BRB)
unnamed: R23.1, R25.2, U5.9 (BRA)
unnamed: R24.1, R26.2, U6.9 (BRA)
unnamed: R27.1, R29.2, U5.25 (BRB)
unnamed: R28.1, R30.2, U6.25 (BRB)
unnamed: U12.3 (1Y), U12.10 (3B)
unnamed: U12.6 (2Y), U12.12 (4A)
unnamed: U12.8 (3Y), U12.13 (4B)
SG_TST: U12.11 (4Y); also elsewhere on the board
SG_TST_E2: U1.38 (SG_TST), U12.9 (3A)
SG_TST_E3: U2.38 (SG_TST), U12.5 (2B)
SG_TST_E4: R4.2, U3.38 (SG_TST), U12.4 (2A)
SG_TST_E5: R19.2, U5.38 (SG_TST), U12.2 (1B)
SG_TST_E6: R20.2, U6.38 (SG_TST), U12.1 (1A)
SPI1_MISO: U1.14 (SDO), U2.14 (SDO), U3.14 (SDO), U5.14 (SDO), U6.14 (SDO); also elsewhere on the board
SPI1_MOSI_BUFF: U1.15 (SDI), U2.15 (SDI), U3.15 (SDI), U5.15 (SDI), U6.15 (SDI); also elsewhere on the board
SPI1_SCK_BUFF_EXP: U1.16 (SCK), U2.16 (SCK), U3.16 (SCK), U5.16 (SCK), U6.16 (SCK); also elsewhere on the board
V_FUSED: C1.1, C2.1, C3.1, C4.1, C5.1, C6.1, C7.1, C8.1, C9.1, C27.1, C28.1, C29.1, C31.1, C32.1, U1.1 (NC), U1.4 (VSA), U1.30 (VSB), U1.33 (NC), U1.36 (VS), U2.1 (NC), U2.4 (VSA), U2.30 (VSB), U2.33 (NC), U2.36 (VS), U3.1 (NC), U3.4 (VSA), U3.30 (VSB), U3.33 (NC), U3.36 (VS), U5.1 (NC), U5.4 (VSA), U5.30 (VSB), U5.33 (NC), U5.36 (VS), U6.1 (NC), U6.4 (VSA), U6.30 (VSB), U6.33 (NC), U6.36 (VS); also elsewhere on the board

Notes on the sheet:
Endstops.
Extruder 5 Stepper Driver
Extruder 3 Stepper Driver
Extruder 2 Stepper Driver
Extruder 6 Stepper Driver
Extruder 4 Stepper Driver
C14 between pin 13 and 17
STALL GUARD OR
R4, R19, R20 - DNP on Duex5 Populate on Duex2
ADD 1nF caps to stepper driver outputs in next version


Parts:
C16, C56: 100u 35V; C_ELEC_6.3x7.7
C17: 0u1 35V; C_0603
C54: 22nF; C_0603
C55, C58: 10u 35V; C_1206
C59, C60, C63: 10u 35V; C_0805
C61: 0u01 35V; C_0603
C62: 100u 25V; C_ELEC_6.3x7.7
C64: 0u1; C_0603
D6, D7: DB2W40300L; D_SOD-123F
J1: E2tp; CONN_3x1
J2: VIN; TERM_2-WAY_6.35mm
J3: E2 MOT; PIN_ARRAY_4x1
J4: E3tp; CONN_3x1
J5: E3 MOT; PIN_ARRAY_4x1
J6: 5V_AUX_IN; PIN_ARRAY_2X1
J7: E4tp; CONN_3x1
J8: E5tp; CONN_3x1
J9: E4 MOT; PIN_ARRAY_4x1
J10: E6tp; CONN_3x1
J11: CONN_01X10; TerminalBlock_Pheonix_PT-3.5mm_10pol
J12: E5 MOT; PIN_ARRAY_4x1
J13: CONN_01X10; Pin_Header_Straight_1x10
J14: E6 MOT; PIN_ARRAY_4x1
J15: FAN/LED 8; PIN_ARRAY_2X1
J16: INPUT; PIN_ARRAY_25X2
J17: 12V; PIN_ARRAY_2X1
J19: E2 TEMP; PIN_ARRAY_2X1
J20: FAN/LED 3; PIN_ARRAY_2X1
J21: E3 TEMP; PIN_ARRAY_2X1
J22: PWM_1; PIN_ARRAY_3X1
J23: FAN/LED 4; PIN_ARRAY_2X1
J24: E4 TEMP; PIN_ARRAY_2X1
J25: FAN/LED 5; PIN_ARRAY_2X1
J26: PWM_2; PIN_ARRAY_3X1
J27: E5 TEMP; PIN_ARRAY_2X1
J28: FAN/LED 6; PIN_ARRAY_2X1
J29: E6 TEMP; PIN_ARRAY_2X1
J30: PWM_3; PIN_ARRAY_3X1
J31: FAN/LED 7; PIN_ARRAY_2X1
J32: PWM_4; PIN_ARRAY_3X1
J33: SPI0; MAX_TEMP_DB
J34: PWM_5; PIN_ARRAY_3X1
J35: E2_STOP; PIN_ARRAY_3X1
J36: E3_STOP; PIN_ARRAY_3X1
J37: E4_STOP; PIN_ARRAY_3X1
J38: E5_STOP; PIN_ARRAY_3X1
J39: E6_STOP; PIN_ARRAY_3X1
JP1: 5V AUX Select; CONN_3x1
JP2: 12V_EN; JUMPER
JP3: Endstop Voltage Select; CONN_3x1
L1: 1uH; C_1210
L2: 10uH; L_6x6
L3: 220 ohm, 3 A; R_0805
L4: MFB-201209-0011PW; R_0805
M1, M2, M3, M9, M10, M11: FID; Fiducial_1mm_Dia_2.54mm_Outer_CopperTop
M4, M5, M6, M7: MOUNTING; Fixing_M4
M8: LOGO Duet; LOGO1
M12: CE; Logo_CE_5mm_mirror
R22: 3K3; R_0603
R31: 22R; R_0603
R46: 200K; R_0603
R68: 10.5K 1%; R_0603
R69, R70: 0R15 0.33W; R_0805
R71: 750R 1%; R_0603
R74: 3R3 0.33W; R_0805
TP3: CONN_01X01; TP_via
U11: A4403; QFN16-4x4

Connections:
5V_S_F: J22.2 (PM), J26.2 (PM), J30.2 (PM), J32.2 (PM), J34.2 (PM), JP1.2 (PM); also elsewhere on the board
12V: C62.1, C63.1, J17.1, L3.2 (B); also elsewhere on the board
+3.3V: J13.2, J16.3, J16.43, J33.8, JP3.3, R22.2; also elsewhere on the board
+5V: J13.1, J16.1, JP1.3, JP3.1; also elsewhere on the board
ADVREF: J16.41; also elsewhere on the board
CS5: J16.50, J33.3
CS6: J16.9, J33.1
CS7: J16.14, J33.7
CS8: J16.19, J33.9
E2-: J11.9; also elsewhere on the board
E2_DIR: J1.2 (PM), J16.6; also elsewhere on the board
E2_EN: J1.3, J16.7; also elsewhere on the board
E2_MOT_1A: J3.2; also elsewhere on the board
E2_MOT_1B: J3.1; also elsewhere on the board
E2_MOT_2A: J3.3; also elsewhere on the board
E2_MOT_2B: J3.4; also elsewhere on the board
E2_PWM: J22.1; also elsewhere on the board
E2_STEP: J1.1, J16.5; also elsewhere on the board
E2_STOP: J35.1; also elsewhere on the board
E3-: J11.7; also elsewhere on the board
E3_DIR: J4.2 (PM), J16.11; also elsewhere on the board
E3_EN: J4.3, J16.12; also elsewhere on the board
E3_MOT_1A: J5.2; also elsewhere on the board
E3_MOT_1B: J5.1; also elsewhere on the board
E3_MOT_2A: J5.3; also elsewhere on the board
E3_MOT_2B: J5.4; also elsewhere on the board
E3_PWM: J26.1; also elsewhere on the board
E3_STEP: J4.1, J16.10; also elsewhere on the board
E3_STOP: J36.1; also elsewhere on the board
E4-: J11.5; also elsewhere on the board
E4_DIR: J7.2 (PM), J16.16; also elsewhere on the board
E4_EN: J7.3, J16.17; also elsewhere on the board
E4_MOT_1A: J9.2; also elsewhere on the board
E4_MOT_1B: J9.1; also elsewhere on the board
E4_MOT_2A: J9.3; also elsewhere on the board
E4_MOT_2B: J9.4; also elsewhere on the board
E4_PWM: J30.1; also elsewhere on the board
E4_STEP: J7.1, J16.15; also elsewhere on the board
E4_STOP: J37.1; also elsewhere on the board
E5-: J11.3; also elsewhere on the board
E5_DIR: J8.2 (PM), J16.21; also elsewhere on the board
E5_EN: J8.3, J16.22; also elsewhere on the board
E5_MOT_1A: J12.2; also elsewhere on the board
E5_MOT_1B: J12.1; also elsewhere on the board
E5_MOT_2A: J12.3; also elsewhere on the board
E5_MOT_2B: J12.4; also elsewhere on the board
E5_PWM: J32.1; also elsewhere on the board
E5_STEP: J8.1, J16.20; also elsewhere on the board
E5_STOP: J38.1; also elsewhere on the board
E6-: J11.1; also elsewhere on the board
E6_DIR: J10.2 (PM), J16.26; also elsewhere on the board
E6_EN: J10.3, J16.27; also elsewhere on the board
E6_MOT_1A: J14.2; also elsewhere on the board
E6_MOT_1B: J14.1; also elsewhere on the board
E6_MOT_2A: J14.3; also elsewhere on the board
E6_MOT_2B: J14.4; also elsewhere on the board
E6_PWM: J34.1; also elsewhere on the board
E6_STEP: J10.1, J16.25; also elsewhere on the board
E6_STOP: J39.1; also elsewhere on the board
ENN: J16.28; also elsewhere on the board
ES_V: J35.2 (PM), J36.2 (PM), J37.2 (PM), J38.2 (PM), J39.2 (PM), JP3.2 (PM); also elsewhere on the board
FAN3-: J20.2 (PM); also elsewhere on the board
FAN4-: J23.2 (PM); also elsewhere on the board
FAN5-: J25.2 (PM); also elsewhere on the board
FAN6-: J28.2 (PM); also elsewhere on the board
FAN7-: J31.2 (PM); also elsewhere on the board
FAN8-: J15.2 (PM); also elsewhere on the board
GND: C16.2, C17.1, C55.2, C56.2, C58.2, C59.2, C60.2, C62.2, C63.2, C64.2, J2.1, J6.1, J13.10, J16.2, J16.30, J16.42, J17.2 (PM), J22.3, J26.3, J30.3, J32.3, J33.2, J34.3, J35.3, J36.3, J37.3, J38.3, J39.3, JP2.1, R69.1, R70.1, R71.1, U11.2 (NC), U11.6 (GND), U11.7 (NC), U11.9 (SGND), U11.13 (NC), U11.14 (NC), U11.15 (NC), U11.16 (NC), U11.17 (PAD); also elsewhere on the board
GPIO1: J13.3; also elsewhere on the board
GPIO2: J13.4; also elsewhere on the board
GPIO3: J13.5; also elsewhere on the board
GPIO4: J13.6; also elsewhere on the board
HEATER3: J16.8; also elsewhere on the board
HEATER4: J16.13; also elsewhere on the board
HEATER5: J16.18; also elsewhere on the board
HEATER6: J16.23; also elsewhere on the board
HEATER7: J16.31; also elsewhere on the board
unnamed: C16.1, C17.2, C58.1, L1.2 (B), L4.1 (A), R46.2, R74.1
unnamed: C54.1, D7.1 (K), L2.1 (A), U11.12 (LX)
unnamed: C54.2, U11.11 (BOOT)
unnamed: C55.1, C56.1, D6.1 (K), L1.1 (A)
unnamed: C59.1, C60.1, C61.1, L2.2 (B), L3.1 (A), R68.2
unnamed: C61.2, R68.1, R71.2, U11.5 (FB)
unnamed: C64.1, U11.4 (SS)
unnamed: D7.2 (A), R69.2, R70.2, U11.8 (Isen)
unnamed: J6.2 (PM), JP1.1
unnamed: J16.32, R31.2
unnamed: JP2.2, U11.10 (DIS)
unnamed: L4.2 (B), R74.2, U11.1 (Vin)
unnamed: R46.1, U11.3 (Ton)
OSCIO: TP3.1; also elsewhere on the board
PB6/TMS: J13.7, J16.29
SG_TST: J16.4; also elsewhere on the board
SPI0_MISO: J16.49, J33.6
SPI0_MOSI: J16.48, J33.5
SPI0_SCK: J16.47, J33.4
SPI1_MISO: J16.34, R22.1; also elsewhere on the board
SPI1_MOSI_BUFF: J16.33; also elsewhere on the board
SPI1_SCK_BUFF_EXP: R31.1; also elsewhere on the board
SX1509_INT: J16.24; also elsewhere on the board
THERMISTOR3: J16.35, J19.2 (PM); also elsewhere on the board
THERMISTOR4: J16.36, J21.2 (PM); also elsewhere on the board
THERMISTOR5: J16.37, J24.2 (PM); also elsewhere on the board
THERMISTOR6: J16.38, J27.2 (PM); also elsewhere on the board
THERMISTOR7: J16.39, J29.2 (PM); also elsewhere on the board
TWCK0: J13.9, J16.46; also elsewhere on the board
TWD0: J13.8, J16.45; also elsewhere on the board
VSSA: J16.40, J19.1, J21.1, J24.1, J27.1, J29.1
V_FAN: J15.1, J20.1, J23.1, J25.1, J28.1, J31.1; also elsewhere on the board
V_FUSED: D6.2 (A), J11.2, J11.4, J11.6, J11.8, J11.10; also elsewhere on the board
V_IN: J2.2 (PM); also elsewhere on the board

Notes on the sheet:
High Current Screw Term
POWER
Heater and Fans
Temperature
Motors
Endstops
Input header (expansion on DuexWifi)
Test Points
All test points are DNP
Servos/PWM Commoned with heater PWM
The E2-E5 test points are not required for ATE however they do provide a point for users to add stp/dir/en headers for external drivers
Port Expander IO
12V Switching power supply

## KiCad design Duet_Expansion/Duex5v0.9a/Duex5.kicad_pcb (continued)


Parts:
C47, C49: 10u 35V; C_1206
C50, C51, C52: 0u1; C_0603
D8: E3 Heat; D_0603
D9: E4 Heat; D_0603
D10: E5 Heat; D_0603
D11: E2 Heat; D_0603
D12, D14, D15, D16, D17, D18: DO-219AB
D13: E6 Heat; D_0603
F1: VIN FUSE; MCCQ-122-minibladefuseholder
J40: CONN_02X03; Pin_Header_Straight_2x03
R3, R47, R48, R49, R50, R51, R52, R53, R66, R72: 1K; R_0603
R32, R33, R34, R35, R36: 4K7; R_0603
R37, R38, R39, R40, R41: 180R; R_0603
R42, R43, R44, R45, R54, R55, R56, R57, R58, R59, R67: 10K; R_0603
R60: 0R DNP; R_0603
R61, R62, R63, R64, R65: 4K7 0.1%; R_0603
R73: 0R; R_0603
TR1, TR2, TR3, TR4, TR5: IPD036N04L; D-PAK
TR6, TR7, TR8, TR9, TR10, TR11: PMV40UN2; SOT-23
U8: SX1509B
U9, U10: 74HCT02; TSSOP-14

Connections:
5V_S_F: J40.1; also elsewhere on the board
12V: J40.4; also elsewhere on the board
+3.3V: C50.1, R3.1, R52.1, R53.1, R54.1, R60.1, U8.4 (VCC1), U8.12 (VDDM), U8.18 (VCC2), U9.2 (1A), U9.3 (1B), U10.2 (1A), U10.3 (1B); also elsewhere on the board
+5V: C51.1, C52.1, R42.1, R43.1, R44.1, R45.1, U9.14 (VCC), U10.14 (VCC); also elsewhere on the board
ADVREF: R61.1, R62.1, R63.1, R64.1, R65.1; also elsewhere on the board
E2-: D11.2 (K), TR1.D; also elsewhere on the board
E2_PWM: R40.2, U10.4 (2Y); also elsewhere on the board
E2_STOP: U8.27 (I/O[0]); also elsewhere on the board
E3-: D8.2 (K), TR2.D; also elsewhere on the board
E3_PWM: R37.2, U10.10 (3Y); also elsewhere on the board
E3_STOP: U8.2 (I/O[3]); also elsewhere on the board
E4-: D9.2 (K), TR3.D; also elsewhere on the board
E4_PWM: R38.2, U10.13 (4Y); also elsewhere on the board
E4_STOP: U8.1 (I/O[2]); also elsewhere on the board
E5-: D10.2 (K), TR4.D; also elsewhere on the board
E5_PWM: R39.2, U9.4 (2Y); also elsewhere on the board
E5_STOP: U8.28 (I/O[1]); also elsewhere on the board
E6-: D13.2 (K), TR5.D; also elsewhere on the board
E6_PWM: R41.2, U9.10 (3Y); also elsewhere on the board
E6_STOP: U8.20 (I/O[13]); also elsewhere on the board
FAN3: R47.2, R55.2, U8.19 (I/O[12])
FAN3-: D15.2 (A), TR6.D; also elsewhere on the board
FAN4: R49.2, R59.1, U8.8 (I/O[7])
FAN4-: D16.2 (A), TR7.D; also elsewhere on the board
FAN5: R50.2, R57.2, U8.7 (I/O[6])
FAN5-: D12.2 (A), TR8.D; also elsewhere on the board
FAN6: R51.2, R58.2, U8.6 (I/O[5])
FAN6-: D14.2 (A), TR9.D; also elsewhere on the board
FAN7: R48.2, R56.2, U8.5 (I/O[4])
FAN7-: D18.2 (A), TR10.D; also elsewhere on the board
FAN8: R67.2, R72.2, U8.22 (I/O[15])
FAN8-: D17.2 (A), TR11.D; also elsewhere on the board
GND: C47.2, C49.2, C50.2, C51.2, C52.2, R55.1, R56.1, R57.1, R58.1, R59.2, R66.2, R67.1, R73.2, TR1.S, TR2.S, TR3.S, TR4.S, TR5.S, TR6.S, TR7.S, TR8.S, TR9.S, TR10.S, TR11.S, U8.3 (GND), U8.17 (GND), U8.26 (ADDR0), U8.PAD (GND), U9.7 (GND), U10.7 (GND); also elsewhere on the board
GPIO1: R42.2, U8.16 (I/O[11]); also elsewhere on the board
GPIO2: R43.2, U8.15 (I/O[10]); also elsewhere on the board
GPIO3: R45.2, U8.14 (I/O[9]); also elsewhere on the board
GPIO4: R44.2, U8.13 (I/O[8]); also elsewhere on the board
HEATER3: U10.5 (2A); also elsewhere on the board
HEATER4: U10.8 (3A); also elsewhere on the board
HEATER5: U10.11 (4A); also elsewhere on the board
HEATER6: U9.5 (2A); also elsewhere on the board
HEATER7: U9.8 (3A); also elsewhere on the board
unnamed: D8.1 (A), R32.1
unnamed: D9.1 (A), R33.1
unnamed: D10.1 (A), R34.1
unnamed: D11.1 (A), R35.1
unnamed: D13.1 (A), R36.1
unnamed: R37.1, TR2.G
unnamed: R38.1, TR3.G
unnamed: R39.1, TR4.G
unnamed: R40.1, TR1.G
unnamed: R41.1, TR5.G
unnamed: R47.1, TR6.G
unnamed: R48.1, TR10.G
unnamed: R49.1, TR7.G
unnamed: R50.1, TR8.G
unnamed: R51.1, TR9.G
unnamed: R54.2, U8.23 (~NRESET)
unnamed: R60.2, R73.1, U8.10 (ADDR1)
unnamed: R66.1, U8.21 (I/O[14])
unnamed: R72.1, TR11.G
unnamed: U9.1 (1Y), U9.6 (2B), U9.9 (3B), U9.11 (4A), U9.12 (4B)
unnamed: U10.1 (1Y), U10.6 (2B), U10.9 (3B), U10.12 (4B)
OSCIO: U8.11 (OSCIO); also elsewhere on the board
SX1509_INT: R3.2, U8.9 (~NINT); also elsewhere on the board
THERMISTOR3: R61.2; also elsewhere on the board
THERMISTOR4: R62.2; also elsewhere on the board
THERMISTOR5: R63.2; also elsewhere on the board
THERMISTOR6: R64.2; also elsewhere on the board
THERMISTOR7: R65.2; also elsewhere on the board
TWCK0: R53.2, U8.25 (SCL); also elsewhere on the board
TWD0: R52.2, U8.24 (SDA); also elsewhere on the board
V_FAN: D12.1 (K), D14.1 (K), D15.1 (K), D16.1 (K), D17.1 (K), D18.1 (K), J40.2, J40.3, J40.6; also elsewhere on the board
V_FUSED: C47.1, C49.1, F1.1, J40.5, R32.2, R33.2, R34.2, R35.2, R36.2; also elsewhere on the board
V_IN: F1.2; also elsewhere on the board

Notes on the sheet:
FAN 3 MOSFET CONTROL
E3 MOSFET CONTROL
E6 MOSFET CONTROL
FAN 4 MOSFET CONTROL
POWER MOSFET DRIVERS
This is a safety feature: if 3.3V gets shorted to ground, the mosfets don't turn on.
FAN 5 MOSFET CONTROL
FAN Voltage Select
E2 MOSFET CONTROL
E4 MOSFET CONTROL
E5 MOSFET CONTROL
FAN 6 MOSFET CONTROL
FAN 7 MOSFET CONTROL
Thermistor Pullups
2bit Board ID in conjunction with I/O[15] R66 is DNP on Duex2
Port Expander
FAN 8 MOSFET CONTROL
Always populate R67, even on Duex2
VIN Fused


Board: 4 copper layers, 100.0 x 123.0 mm, 246 parts (1 on the bottom side), 181 nets.

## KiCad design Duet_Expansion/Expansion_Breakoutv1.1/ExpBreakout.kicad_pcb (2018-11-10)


Board: 2 copper layers, 88.5 x 28.0 mm, 22 parts (0 on the bottom side), 53 nets.

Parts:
C1, C2, C3, C4, C5: 0u1; C_0603
J1: EXPANSION; PIN_ARRAY_25X2
M4, M5, M6, M7: MOUNTING; Fixing_M4
P1: E2; PIN_ARRAY_6x1
P2: E3; PIN_ARRAY_6x1
P3: E4; PIN_ARRAY_6x1
P4: E5; PIN_ARRAY_6x1
P5: E6; PIN_ARRAY_6x1
P6: H6_PWM; PIN_ARRAY_3X1
P7: H7_PWM; PIN_ARRAY_3X1
U1, U2, U3, U4: 75ALS192; SOIC-16_3.9x9.9mm_Pitch1.27mm
U5: 74HCT02; TSSOP-14

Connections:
+3.3V: J1.3, J1.43, U5.2, U5.3
+5V: C1.1, C2.1, C3.1, C4.1, C5.1, J1.1, P6.2, P7.2, U1.16, U2.16, U3.16, U4.16, U5.14
E2_DIR: J1.6, U1.7
E2_D_OUT_Y: P1.3, U1.6
E2_D_OUT_Z: P1.4, U1.5
E2_EN: J1.7, U1.15
E2_E_OUT_Y: P1.6, U1.14
E2_E_OUT_Z: P1.5, U1.13
E2_STEP: J1.5, U1.1
E2_S_OUT_Y: P1.1, U1.2
E2_S_OUT_Z: P1.2, U1.3
E3_DIR: J1.11, U2.1
E3_D_OUT_Y: P2.3, U2.2
E3_D_OUT_Z: P2.4, U2.3
E3_EN: J1.12, U2.15
E3_E_OUT_Y: P2.6, U2.14
E3_E_OUT_Z: P2.5, U2.13
E3_STEP: J1.10, U1.9
E3_S_OUT_Y: P2.1, U1.10
E3_S_OUT_Z: P2.2, U1.11
E4_DIR: J1.16, U2.9
E4_D_OUT_Y: P3.3, U2.10
E4_D_OUT_Z: P3.4, U2.11
E4_EN: J1.17, U3.1
E4_E_OUT_Y: P3.6, U3.2
E4_E_OUT_Z: P3.5, U3.3
E4_STEP: J1.15, U2.7
E4_S_OUT_Y: P3.1, U2.6
E4_S_OUT_Z: P3.2, U2.5
E5_DIR: J1.21, U3.7
E5_D_OUT_Y: P4.3, U3.6
E5_D_OUT_Z: P4.4, U3.5
E5_EN: J1.22, U3.9
E5_E_OUT_Y: P4.6, U3.10
E5_E_OUT_Z: P4.5, U3.11
E5_STEP: J1.20, U3.15
E5_S_OUT_Y: P4.1, U3.14
E5_S_OUT_Z: P4.2, U3.13
E6_DIR: J1.26, U4.15
E6_D_OUT_Y: P5.3, U4.14
E6_D_OUT_Z: P5.4, U4.13
E6_EN: J1.27, U4.7
E6_E_OUT_Y: P5.6, U4.6
E6_E_OUT_Z: P5.5, U4.5
E6_STEP: J1.25, U4.1
E6_S_OUT_Y: P5.1, U4.2
E6_S_OUT_Z: P5.2, U4.3
GND: C1.2, C2.2, C3.2, C4.2, C5.2, J1.2, J1.30, J1.42, P6.3, P7.3, U1.4, U1.8, U1.12, U2.4, U2.8, U2.12, U3.4, U3.8, U3.12, U4.4, U4.8, U4.9, U4.12, U5.7
HEATER6: J1.23, U5.5
HEATER6_PWM: P6.1, U5.4
HEATER7: J1.31, U5.8
HEATER7_PWM: P7.1, U5.10
unnamed: U5.1, U5.6, U5.9, U5.11, U5.12

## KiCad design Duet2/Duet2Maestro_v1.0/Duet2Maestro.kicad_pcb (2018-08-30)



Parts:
C9, C11, C32, C33, C84: 2u2; C_0603
C14, C21, C56, C57, C92: 22n X7R 10% 16V; C_0603
C15, C26, C34, C35, C55, C86: 0u1; C_0603
C17, C28, C36, C37, C87: 0.1u 50V; C_0603
C20, C23, C24, C38, C39, C59, C60, C75, C89, C93: 0u1 50V; C_0603
C22, C31, C78, C83, C104: 100u 35V; C_ELEC_6.3x7.7
C25, C27, C29, C30, C63, C65, C71, C72, C73, C74, C76, C77, C85, C88, C100, C101, C102, C103, C107, C113: 470p 100V; C_0603
C40, C41, C42, C43, C111: 2n2; C_0603
C90: 0u01; C_0603
D2, D9, D10: BAT54C; SOT-23-D
R4, R5, R8, R9, R28: 22K; R_0603
R6, R7, R17, R18, R26, R27, R29, R32, R33, R34: 0R075 1% 0.33W; R_0603_Large_Pads
R30: 1K; R_0603
R56, R57, R58, R59, R62, R69, R70, R71, R72, R95, R96: 10K; R_0603
U1: E0_MOT; QFN-28-1EP_5x5mm_Pitch0.5mm
U4: X_MOT; QFN-28-1EP_5x5mm_Pitch0.5mm
U5: E1_MOT; QFN-28-1EP_5x5mm_Pitch0.5mm
U6: Y_MOT; QFN-28-1EP_5x5mm_Pitch0.5mm
U7: Z_MOT; QFN-28-1EP_5x5mm_Pitch0.5mm
U8: SN74CB3Q3251; QSOP-16_3.9x4.9mm_Pitch0.635mm

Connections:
+3.3V: C15.1, C26.1, C34.1, C35.1, C55.1, C86.1, D2.3, D9.3, D10.3, R4.1, R5.1, R8.1, R9.1, R28.1, R69.2, R70.2, R71.2, R72.2, R96.2, U1.19 (VCC_IO), U4.19 (VCC_IO), U5.19 (VCC_IO), U6.19 (VCC_IO), U7.19 (VCC_IO), U8.16 (VCC); also elsewhere on the board
E0_DIR: U1.23 (DIR); also elsewhere on the board
E0_MOT_A1: C25.2, U1.10 (OA1); also elsewhere on the board
E0_MOT_A2: C27.2, U1.8 (OA2); also elsewhere on the board
E0_MOT_B1: C29.2, U1.11 (OB1); also elsewhere on the board
E0_MOT_B2: C30.2, U1.13 (OB2); also elsewhere on the board
E0_STEP: U1.25 (STEP); also elsewhere on the board
E0_STOP: C43.1, D9.1, R59.1; also elsewhere on the board
E0_STOP_CONN: R59.2, R71.1; also elsewhere on the board
E0_UART: R4.2, U1.20 (PDN_UART), U8.1 (B4); also elsewhere on the board
E1_DIR: U5.23 (DIR); also elsewhere on the board
E1_MOT_A1: C63.2, U5.10 (OA1); also elsewhere on the board
E1_MOT_A2: C65.2, U5.8 (OA2); also elsewhere on the board
E1_MOT_B1: C71.2, U5.11 (OB1); also elsewhere on the board
E1_MOT_B2: C72.2, U5.13 (OB2); also elsewhere on the board
E1_STEP: U5.25 (STEP); also elsewhere on the board
E1_STOP: C111.1, D10.1, R95.1; also elsewhere on the board
E1_STOP_CONN: R95.2, R96.1; also elsewhere on the board
E1_UART: R8.2, U5.20 (PDN_UART), U8.15 (B5); also elsewhere on the board
E2_UART: U8.14 (B6); also elsewhere on the board
E3_UART: U8.13 (B7); also elsewhere on the board
ENN: U1.24 (~ENN), U4.24 (~ENN), U5.24 (~ENN), U6.24 (~ENN), U7.24 (~ENN); also elsewhere on the board
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

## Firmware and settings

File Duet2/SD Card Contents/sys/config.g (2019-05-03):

; Configuration file for factory testing Duet Ethernet and Wifi with V2.02 firmware

*******************************************************************************************************************
FOR TESTING ONLY! USE https://configurator.reprapfirmware.org/ to generate configuration files for your printer!
*******************************************************************************************************************


; Communication and general
M111 S0                            		; Debug off
M550 PDuetTest					; Machine name and Netbios name (can be anything you like)
M551 Preprap                   			; Machine password (used for FTP)

*** Ethernet networking: The following lines are used for factory testing - PLEASE REMOVE THEM
M540 P0xBE:0xEF:0xDE:0xAD:0xFE:0xED		; MAC Address
M552 P192.168.1.14				; IP address
M554 P192.168.1.255				; Gateway
M553 P255.255.255.0				; Netmask

;*** End of factory test lines to be removed

;*** Networking
M552 S1						; Turn network on

M555 P2						; Set output to look like Marlin
G21						; Work in millimetres
G90						; Send absolute coordinates...
M83						; ...but relative extruder moves

; Disable Fan 1 thermostatic mode
M106 P1 H-1

; Axis and motor configuration
M569 P0 S1					; Drive 0 goes forwards
M569 P1 S1					; Drive 1 goes forwards
M569 P2 S1					; Drive 2 goes forwards
M569 P3 S1					; Drive 3 goes forwards
M569 P4 S1					; Drive 4 goes forwards
M574 X2 Y2 Z2 S1				; set endstop configuration (all endstops at high end, active high)
;*** The homed height is deliberately set too high in the following - you will adjust it during calibration
M665 R105.6 L215.0 B85 H250			; set delta radius, diagonal rod length, printable radius and homed height
M666 X0 Y0 Z0					; put your endstop adjustments here, or let auto calibration find them
M350 X16 Y16 Z16 E16:16 I1			; Set 16x microstepping with interpolation
M92 X80 Y80 Z80					; Set axis steps/mm
M906 X1000 Y1000 Z1000 E800 I60			; Set motor currents (mA) and increase idle current to 60%
M201 X1000 Y1000 Z1000 E1000			; Accelerations (mm/s^2)
M203 X20000 Y20000 Z20000 E3600			; Maximum speeds (mm/min)
M566 X1200 Y1200 Z1200 E1200			; Maximum instant speed changes mm/minute

; Thermistors
M305 P0 T100000 B3950 R4700 H30 L0		; Put your own H and/or L values here to set the bed thermistor ADC correction
M305 P1 T100000 B3974 R4700 H30 L0		; Put your own H and/or L values here to set first nozzle thermistor ADC correction
M305 P2 T100000 B3974 R4700 H30 L0		; Put your own H and/or L values here to set 2nd nozzle thermistor ADC correction

M570 S180					; Hot end may be a little slow to heat up so allow it 180 seconds

; Adjustments for dummy heaters on test rig
M307 H0 A250 C140 D5.5 B1
M307 H1 A250 C140 D5.5 B0
M307 H2 A250 C140 D5.5 B0

; Fans
M106 P1 S-1					; disable thermostatic mode for fan 1

; Tool definitions
M563 P0 D0 H1					; Define tool 0
G10 P0 S0 R0					; Set tool 0 operating and standby temperatures
;*** If you have a single-nozzle build, comment the next 2 lines
M563 P1 D1 H2					; Define tool 1
G10 P1 S0 R0					; Set tool 1 operating and standby temperatures
M92 E80:80					; Set extruder steps per mm

; Z probe and compensation definition
;*** If you have a switch instead of an IR probe, change P1 to P4 in the following M558 command. 
M558 P5 F100 T6000 X0 Y0 Z0 H3			; Z probe is a Smart Effector and is not used for homing any axes R0.4 not used. Reduced F300 to 100
G31 P100 X0 Y0 Z-0.25				; Set the zprobe height and threshold for Smart Effector

;*** If you are using axis compensation, put the figures in the following command
M556 S78 X0 Y0 Z0				; Axis compensation here

M208 S1 Z-0.2					; set minimum Z

T0						; select first hot end
; M117 Use https://configurator.reprapfirmware.org/ to set up your printer config

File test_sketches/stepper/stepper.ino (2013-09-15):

/*
Test code for A4982 Stepper drivers on DUET 0.3,0.40.5 and expansion board 0.1

The Vref is set first, note the peculiarity with the values reversed for Pot1 and 2 vs Pot 3 and 4, this only applies to Duet 0.3

Channel 0:  0x0 = Vref High (~1,6V), 0x100 = Vref Off, 0x80 = Vref 50% (~0.8V)
Channel 1:  0x0 = Vref High (~1,6V), 0x100 = Vref Off, 0x80 = Vref 50% (~0.8V)
Channel 2:  0x0 = Vref Off, 0x100 = Vref High (~1,6V), 0x80 = Vref 50% (~0.8V)
Channel 3:  0x0 = Vref Off, 0x100 = Vref High (~1,6V), 0x80 = Vref 50% (~0.8V)

On Duet 0.4 and later and expansion board:

Channel 0:  0x0 = Vref Off, 0x100 = Vref High (~1,6V), 0x80 = Vref 50% (~0.8V)
Channel 1:  0x0 = Vref Off, 0x100 = Vref High (~1,6V), 0x80 = Vref 50% (~0.8V)
Channel 2:  0x0 = Vref Off, 0x100 = Vref High (~1,6V), 0x80 = Vref 50% (~0.8V)
Channel 3:  0x0 = Vref Off, 0x100 = Vref High (~1,6V), 0x80 = Vref 50% (~0.8V)

This code then steps all 4 axis almost simultaneously CW then CCW slower then faster
If an expansion board is defined it add the expansion board axis into the order.

The values for delayMicroseconds work with 1/16th microstepping
extend the delays for larger microsteps.

If the end stops are not connected by a NC switch or wire short then set the relavent endStopDisabled=true
to disable the checking for them

For the E0_En and Z_EN pins the "SamNonDuePin" libaray allows access to pins that are not defined in the Arduino
Due software but are provided by the SAM3X8E, this library is still in development.

Various pins are not defined, or defined differently on the Arduino Due so the SamNonDuePin library is used to access them as standard I/O

*/
#include "Arduino.h"
#include <Wire.h>
#include "MCP4461.h"
#include "SamNonDuePin.h"

#define EXPANSION

MCP4461 mcp_duet(0x2C);

#ifdef EXPANSION
MCP4461 mcp_exp(0x2E);
#endif

//digipot resistance values
//0x0 = Vref Off, 0x100 = Vref High (~1,6V), 0x80 = Vref 50% (~0.8V)
#define E0_POT_R 0x80
#define X_POT_R 0x80 
#define Z_POT_R 0x80
#define Y_POT_R 0x80
#define E1_POT_R 0x80
#define E2_POT_R 0x80
#define E3_POT_R 0x80
#define E4_POT_R 0x80

#define X_STEP 14
#define X_DIR 15
#define X_EN 29
#define X_STOP 11

#define Y_STEP 25
#define Y_DIR 26
#define Y_EN 27
#define Y_STOP 28

#define Z_STEP 5
#define Z_DIR 4
#define Z_EN X1//Sam pin PC27 not defined for Due
#define Z_STOP 60

#define E0_STEP X2 //Sam pin configured for CAN on Due
#define E0_DIR X3 //Sam pin configured for CAN on Due
#define E0_EN  X0//Sam pin pin PA5 not defined for Due
#define E0_STOP 31

#ifdef EXPANSION
#define E1_STEP 41
#define E1_DIR 35
#define E1_EN  37
#define E1_STOP 24

#define E2_STEP 39
#define E2_DIR 53
#define E2_EN  X8
#define E2_STOP 46

#define E3_STEP X4
#define E3_DIR 51
#define E3_EN  50
#define E3_STOP 45

#define E4_STEP 49
#define E4_DIR 48
#define E4_EN  47
#define E4_STOP 44
#endif

//use to disable the axis endstop checking code so the motors step regardless
boolean XendStopDisabled = true;
boolean YendStopDisabled = true;
boolean ZendStopDisabled = true;
boolean E0endStopDisabled = true;
#ifdef EXPANSION
boolean E1endStopDisabled = true;
boolean E2endStopDisabled = true;
boolean E3endStopDisabled = true;
boolean E4endStopDisabled = true;
#endif

void setup() {
 //setup the Vrefs input to the stepper drivers
 //start the I2C comms with the digipot
 mcp_duet.begin();
 //set both volatile and non volatile wipers
 mcp_duet.setVolatileWiper(0,E0_POT_R);  mcp_duet.setNonVolatileWiper(0,E0_POT_R);
 mcp_duet.setVolatileWiper(1,X_POT_R);  mcp_duet.setNonVolatileWiper(1,X_POT_R);
 mcp_duet.setVolatileWiper(2,Z_POT_R);  mcp_duet.setNonVolatileWiper(2,Z_POT_R);
 mcp_duet.setVolatileWiper(3,Y_POT_R);  mcp_duet.setNonVolatileWiper(3,Y_POT_R);
 #ifdef EXPANSION
 mcp_exp.begin();
 mcp_exp.setVolatileWiper(0,E1_POT_R);  mcp_exp.setNonVolatileWiper(0,E1_POT_R);
 mcp_exp.setVolatileWiper(0,E2_POT_R);  mcp_exp.setNonVolatileWiper(0,E2_POT_R);
 mcp_exp.setVolatileWiper(0,E3_POT_R);  mcp_exp.setNonVolatileWiper(0,E3_POT_R);
 mcp_exp.setVolatileWiper(0,E4_POT_R);  mcp_exp.setNonVolatileWiper(0,E4_POT_R);
 #endif
 
 //Setup the pins for the Stepper drivers
 pinMode(X_STEP, OUTPUT);
 pinMode(X_DIR, OUTPUT);
 pinMode(X_EN, OUTPUT);
 pinMode(X_STOP, INPUT);
 
 pinMode(Y_STEP, OUTPUT);
 pinMode(Y_DIR, OUTPUT);
 pinMode(Y_EN, OUTPUT);
 pinMode(Y_STOP, INPUT);
 
 pinMode(Z_STEP, OUTPUT);
 pinMode(Z_DIR, OUTPUT);
 pinModeNonDue(Z_EN, OUTPUT);
 pinMode(Z_STOP, INPUT);
 
 pinModeNonDue(E0_STEP, OUTPUT);
 pinModeNonDue(E0_DIR, OUTPUT);
 pinModeNonDue(E0_EN, OUTPUT);
 pinMode(E0_STOP, INPUT);
#ifdef EXPANSION
 pinMode(E1_STEP, OUTPUT);
 pinMode(E1_DIR, OUTPUT);
 pinMode(E1_EN, OUTPUT);
 pinMode(E1_STOP, INPUT);
 
 pinMode(E2_STEP, OUTPUT);
 pinMode(E2_DIR, OUTPUT);
 pinModeNonDue(E2_EN, OUTPUT);
 pinMode(E2_STOP, INPUT);
 
 pinModeNonDue(E3_STEP, OUTPUT);
 pinMode(E3_DIR, OUTPUT);
 pinMode(E3_EN, OUTPUT);
 pinMode(E3_STOP, INPUT);
 
 pinMode(E4_STEP, OUTPUT);
 pinMode(E4_DIR, OUTPUT);
 pinMode(E4_EN, OUTPUT);
 pinMode(E4_STOP, INPUT);
#endif

//disable the steppers to begin
  digitalWrite(X_EN, HIGH);
  digitalWrite(Y_EN, HIGH);
  digitalWriteNonDue(Z_EN, HIGH);
  digitalWriteNonDue(E0_EN, HIGH);
#ifdef EXPANSION
  digitalWrite(E1_EN, HIGH);
  digitalWriteNonDue(E2_EN, HIGH);
  digitalWrite(E3_EN, HIGH);
  digitalWrite(E4_EN, HIGH);
#endif
}

void loop() {
  
  //enable the steppers
  digitalWrite(X_EN, LOW);
  digitalWrite(Y_EN, LOW);
  digitalWriteNonDue(Z_EN, LOW);
  digitalWriteNonDue(E0_EN, LOW);
#ifdef EXPANSION
  digitalWrite(E1_EN, LOW);
  digitalWriteNonDue(E2_EN, LOW);
  digitalWrite(E3_EN, LOW);
  digitalWrite(E4_EN, LOW);
#endif
  
  //CW 
  digitalWrite(X_DIR, HIGH);
  digitalWrite(Y_DIR, HIGH);
  digitalWrite(Z_DIR, HIGH);
  digitalWriteNonDue(E0_DIR, HIGH);
#ifdef EXPANSION
  digitalWrite(E1_DIR, HIGH);
  digitalWrite(E2_DIR, HIGH);
  digitalWrite(E3_DIR, HIGH);
  digitalWrite(E4_DIR, HIGH);
#endif
  
  for (int i = 1 ; i<5000 ;i++) { 
    if(digitalRead(X_STOP) == 0 || XendStopDisabled) digitalWrite(X_STEP, HIGH);
    if(digitalRead(Y_STOP) == 0 || YendStopDisabled) digitalWrite(Y_STEP, HIGH);
    if(digitalRead(Z_STOP) == 0 || ZendStopDisabled) digitalWrite(Z_STEP, HIGH);
    if(digitalRead(E0_STOP) == 0 || E0endStopDisabled)  digitalWriteNonDue(E0_STEP, HIGH);
#ifdef EXPANSION
    if(digitalRead(E1_STOP) == 0 || E1endStopDisabled)  digitalWrite(E1_STEP, HIGH);
    if(digitalRead(E2_STOP) == 0 || E2endStopDisabled)  digitalWrite(E2_STEP, HIGH);
    if(digitalRead(E3_STOP) == 0 || E3endStopDisabled)  digitalWriteNonDue(E3_STEP, HIGH);
    if(digitalRead(E4_STOP) == 0 || E4endStopDisabled)  digitalWrite(E4_STEP, HIGH);
#endif  
    delayMicroseconds(90);
    if(digitalRead(X_STOP) == 0 || XendStopDisabled) digitalWrite(X_STEP, LOW);
    if(digitalRead(Y_STOP) == 0 || YendStopDisabled) digitalWrite(Y_STEP, LOW);
    if(digitalRead(Z_STOP) == 0 || ZendStopDisabled) digitalWrite(Z_STEP, LOW);
    if(digitalRead(E0_STOP) == 0 || E0endStopDisabled)  digitalWriteNonDue(E0_STEP, LOW);
#ifdef EXPANSION
    if(digitalRead(E1_STOP) == 0 || E1endStopDisabled)  digitalWrite(E1_STEP, LOW);
    if(digitalRead(E2_STOP) == 0 || E2endStopDisabled)  digitalWrite(E2_STEP, LOW);
    if(digitalRead(E3_STOP) == 0 || E3endStopDisabled)  digitalWriteNonDue(E3_STEP, LOW);
    if(digitalRead(E4_STOP) == 0 || E4endStopDisabled)  digitalWrite(E4_STEP, LOW);
#endif
    delayMicroseconds(90);
  }
  //disable the steppers
  digitalWrite(X_EN, HIGH);
  digitalWrite(Y_EN, HIGH);
  digitalWriteNonDue(Z_EN, HIGH);
  digitalWriteNonDue(E0_EN, HIGH);
#ifdef EXPANSION
  digitalWrite(E1_EN, HIGH);
  digitalWriteNonDue(E2_EN, HIGH);
  digitalWrite(E3_EN, HIGH);
  digitalWrite(E4_EN, HIGH);
#endif
  
  delay(1000);
  
  //enable the steppers
  digitalWrite(X_EN, LOW);
  digitalWrite(Y_EN, LOW);
  digitalWriteNonDue(Z_EN, LOW);
  digitalWriteNonDue(E0_EN, LOW);
#ifdef EXPANSION
  digitalWrite(E1_EN, LOW);
  digitalWriteNonDue(E2_EN, LOW);
  digitalWrite(E3_EN, LOW);
  digitalWrite(E4_EN, LOW);
#endif
 
  //CCW
  digitalWrite(X_DIR, LOW);
  digitalWrite(Y_DIR, LOW);
  digitalWrite(Z_DIR, LOW);
  digitalWriteNonDue(E0_DIR, LOW);
#ifdef EXPANSION
  digitalWrite(E1_DIR, LOW);
  digitalWrite(E2_DIR, LOW);
  digitalWrite(E3_DIR, LOW);
  digitalWrite(E4_DIR, LOW);
#endif
  
  for (int i = 1 ; i<5000 ;i++)
  { 
    if(digitalRead(X_STOP) == 0 || XendStopDisabled) digitalWrite(X_STEP, HIGH);
    if(digitalRead(Y_STOP) == 0 || YendStopDisabled) digitalWrite(Y_STEP, HIGH);
    if(digitalRead(Z_STOP) == 0 || ZendStopDisabled) digitalWrite(Z_STEP, HIGH);
    if(digitalRead(E0_STOP) == 0 || E0endStopDisabled)  digitalWriteNonDue(E0_STEP, HIGH);
#ifdef EXPANSION
    if(digitalRead(E1_STOP) == 0 || E1endStopDisabled)  digitalWrite(E1_STEP, HIGH);
    if(digitalRead(E2_STOP) == 0 || E2endStopDisabled)  digitalWrite(E2_STEP, HIGH);
    if(digitalRead(E3_STOP) == 0 || E3endStopDisabled)  digitalWriteNonDue(E3_STEP, HIGH);
    if(digitalRead(E4_STOP) == 0 || E4endStopDisabled)  digitalWrite(E4_STEP, HIGH);
#endif 
    delayMicroseconds(100);
    if(digitalRead(X_STOP) == 0 || XendStopDisabled) digitalWrite(X_STEP, LOW);
    if(digitalRead(Y_STOP) == 0 || YendStopDisabled) digitalWrite(Y_STEP, LOW);
    if(digitalRead(Z_STOP) == 0 || ZendStopDisabled) digitalWrite(Z_STEP, LOW);
    if(digitalRead(E0_STOP) == 0 || E0endStopDisabled) digitalWriteNonDue(E0_STEP, LOW);
#ifdef EXPANSION
    if(digitalRead(E1_STOP) == 0 || E1endStopDisabled)  digitalWrite(E1_STEP, LOW);
    if(digitalRead(E2_STOP) == 0 || E2endStopDisabled)  digitalWrite(E2_STEP, LOW);
    if(digitalRead(E3_STOP) == 0 || E3endStopDisabled)  digitalWriteNonDue(E3_STEP, LOW);
    if(digitalRead(E4_STOP) == 0 || E4endStopDisabled)  digitalWrite(E4_STEP, LOW);
#endif
    delayMicroseconds(100);
  }
  //disable the steppers
  digitalWrite(X_EN, HIGH);
  digitalWrite(Y_EN, HIGH);
  digitalWriteNonDue(Z_EN, HIGH);
  digitalWriteNonDue(E0_EN, HIGH);
#ifdef EXPANSION
  digitalWrite(E1_EN, HIGH);
  digitalWrite(E2_EN, HIGH);
  digitalWrite(E3_EN, HIGH);
  digitalWrite(E4_EN, HIGH);
#endif
  delay(1000);
}

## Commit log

2013-04-11 Added analog input test code
    The ADC calcs.txt shows the theoretical ADC values based on the nominal
    resistance from an EPCOS B57560G104F thermistor with a Vanalog of 3.3V,
    measured with an ADC resolution of 10bits.
2013-04-15 LwIP Example Added
    Adapted from the Atmel Studio Framework example for SAM3X-EK:
    http://www.atmel.com/tools/AVRSOFTWAREFRAMEWORK.aspx
    More info on LwIP can be found here
    http://lwip.wikia.com/wiki/LwIP_Wiki
2013-04-16 Undefined Due pins example
    The stepper sketch has been updated to move all 4 steppers and to work
    with the
    UdefDuePin library which is the beginnings of a library to access the
    SAM3X8E pins that are not defined by the Arduino software
2013-04-18 Added E1 example on expansion header pins
    To allow for testing and comparison of other stepper driver chips and
    boards three expansion header pins(PC14,PC15,PC16) are configured as
    E1_DIR, E1_STEP and E1_EN.
2013-04-25 PWM demonstration in FETs.ino
    Updated the UdefDuePin library to carry out analog write on SAM3X8E PWM
    pins that are not defined within the default arduino pin allocations.
2013-05-28 Removed printf statements and other minor changes
    Reduced the compile size of the library by commenting out printf
    statements.
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2013-12-02 Duet 0.6 added
    For more info check out www.think3dprint3d.com/duet
    [Comms.sch, Duet0.6.brd, Duet0.6.sch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]
2013-12-02 Expansion Board v0.2 Added
    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
    [Duet_expansion0.2.brd, Duet_expansion0.2.sch, Headers_expansion.sch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]
2013-12-30 Added Duet0.3 archive files
    Info here:
    http://blog.think3dprint3d.com/2013/12/duet-fet-psu-and-steppertesting.html
    [Comms.sch, Duet0.3.brd, Duet0.3.sch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]
2014-01-15 Duet 0.4 design files added to archive
    [Comms.sch, Duet0.4 BOM.xls, Duet0.4.brd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]
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2015-04-12 Changed folder structure
    [Duet_expansion0.2.brd, Duet_expansion0.2.sch, Headers_expansion.sch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]
2015-04-12 Duex4 v0.2a KiCAD files
    [Duetx4.brd, Duetx4.sch, Headers_expansion.sch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]
2015-08-06 Rename Duet to Duet0.6
    Rename in prep for Duet0.8.5 upload
    [Comms.sch, Duet0.6.brd, Duet0.6.sch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]
2015-08-07 Duet0.8.5 KiCAD source files
    The source files for the Duet 0.8.5 3d printer electronics design.
    Licensed under the CERN OHL v1.2
    [Comms.sch, Duet0.85.brd, Duet0.85.sch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]
2016-04-11 Re-arranged directory structure
    [Duet_expansion0.2.brd, Duet_expansion0.2.sch, Headers_expansion.sch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]
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2016-08-28 DuetWifiv1.0 Initial Commit
    The DuetWifi hardware design files in KiCAD. For details on the Duet
    wifi see the README file
    [Comms.sch, DuetWifi.kicad_pcb, DuetWifi.sch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]
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2017-01-06 Schematic footprint error correction
    The schematic specified the SAM3X8E footprint as a LQFP100. this
    corrects this to LQFP144
    [Processor.sch]
2017-01-12 Added Duex2/5 Source
    [Comms.sch, Duex5.kicad_pcb, Duex5.sch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]
2017-01-30 Added V1.01 Sources
    [Comms.sch, DuetWifi.kicad_pcb, DuetWifi.sch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]
2017-04-20 Added DuetWifi v1.02 KiCAD files
    And updated directory structure
    [Comms.sch, DuetWifi.kicad_pcb, DuetWifi.sch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]
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2017-04-20 Duet Ethernet Module
    [DuetEthernet.kicad_pcb, DuetEthernet.sch]
2017-07-12 Added Duex5_v0.8
    [Comms.sch, Duex5.kicad_pcb, Duex5.sch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]
2017-07-13 Added Expansion Breakout v1.0 source files
    [ExpBreakout.kicad_pcb, ExpBreakout.sch]
2017-10-08 SD Card Contents
    As at August 2017. Read the readme
    [bed.g, cancel.g, config.g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]
2017-10-08 add gcodes folder
    empty folder not added intially
    [test.g]
2017-12-25 Directory refactoring
    Clarified the Duet 2 (Wifi or bare board + Ethernet Module) version structure.
    [Comms.sch, DuetEthernet.kicad_pcb, DuetEthernet.sch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]
2017-12-25 Duet2v1.03 source files published
    Minor updates see https://duet3d.com/wiki/Hardware_overview#Version_History for changes from previous versions.
    [Comms.sch, Duet2.kicad_pcb, Duet2.sch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]
2018-08-23 SD card contents updated
    [config.g]
2018-08-30 Duet 2 Maestro source files
    [Comms.sch, Duet2Maestro.kicad_pcb, Duet2Maestro.sch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]
2018-10-27 Archived Obsolete Duet Designs
    [Comms.sch, Duet0.6.brd, Duet0.6.sch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]
2018-10-27 Archived Obsolete Duex Files
    [Duetx4.brd, Duetx4.sch, Headers_expansion.sch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]
2018-10-27 archived v1.03
    [Comms.sch, Duet2.kicad_pcb, Duet2.sch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]
2018-11-10 Rename to v1.1
    Expansion Breakout board version was incorrect at v1.0 (that was a in house development version) Verison 1.1 is the shipped version.
    [ExpBreakout.kicad_pcb, ExpBreakout.sch]
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2019-05-03 Updated default SD card contents
    [config.g, test.g]
2019-07-01 Duex5v0.9
    The PCB revision 0.9a update for Duex 2 and Duex 5 v0.9 and v0.9a
    [Duex5-2019-01-18-19-23-53.sch, Duex5-2019-07-01-20-17-27.sch, Duex5.kicad_pcb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]
2019-07-21 Fixed errors in wiring diagram
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2020-02-07 Ethernet Module Kicad project added
    [EthernetModule.kicad_pcb, EthernetModule.sch]
2020-04-15 Create Duet2Maestro_Wiring_V1.0_drawing_v1.2.svg
    new drawing version fixing thermistor labelling
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2022-05-01 Added Duexv0.11 KiCAD files
    [Duex5.kicad_pcb, Duex5.sch, Headers.sch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]
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2023-07-24 added v1.05 KiCAD source
    [Comms.sch, Duet2.kicad_pcb, Duet2.sch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]
2023-11-27 v1.06 KiCAD project Files
    [Comms.kicad_sch, Duet2.kicad_sch, Headers.kicad_sch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]
2024-06-10 IR sensor STEP
    [MiniLedSensor.stp]
